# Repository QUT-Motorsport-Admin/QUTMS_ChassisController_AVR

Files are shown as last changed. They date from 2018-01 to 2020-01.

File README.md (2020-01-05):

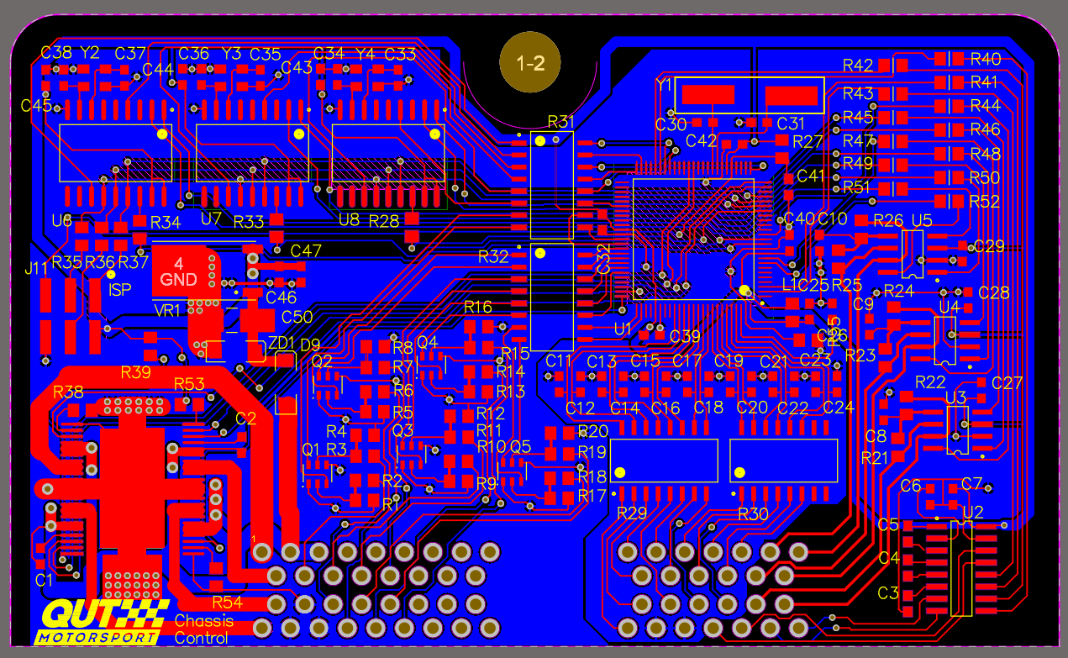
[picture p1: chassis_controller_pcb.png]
PCB Image


# Chassis Controller

The role of the chassis controller is to manage and coordinate all of the electrical systems on the car. At regular intervals it reads inputs and monitors devices on the car, checking they are responding to heartbeat messages within a specified time.

## Features

- 3 CANBUS interfaces using the MCP2515 controller
- 2 UART serial interfaces
- 14 analog inputs
- 9 digital inputs
- Dual 5A H-bridge throttle controller
- 60 pin MoTeC compatible connector

## System Architecture

### Serial Communication
The chassis controller has two UART interfaces, one which is dedicated to debugging. There is a [specification](https://docs.google.com/spreadsheets/d/1M0LFDXtBvufXvVOvwZmF34SnBRF86Ai6lYGNQQMeDdA/edit?usp=sharing "QUTMS_UART_Packet_Def") for a protocol to be used when the chassis controller is communicating with configuration software.

### Block Diagram

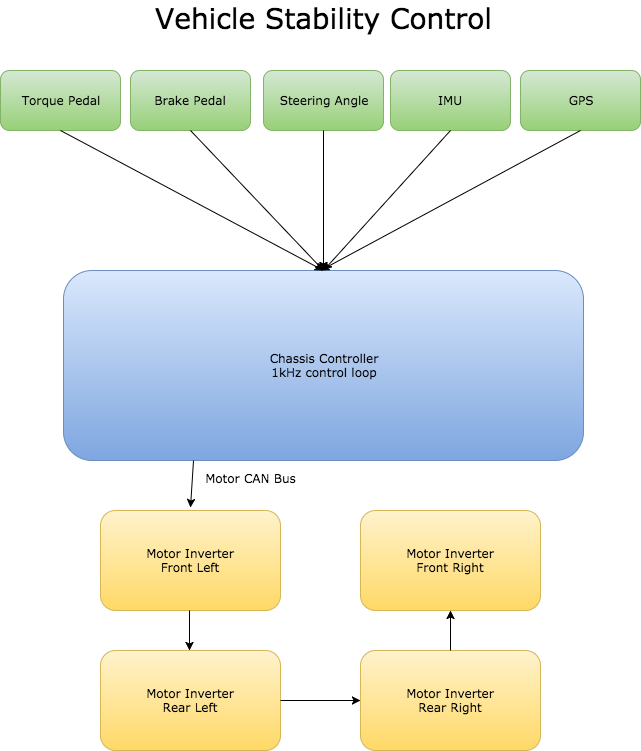
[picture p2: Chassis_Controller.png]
RoughOutline


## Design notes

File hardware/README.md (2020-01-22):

# Chassis Controller Hardware

## RS232 Serial Connection
Useful for getting debug output from the microcontroller. Uses a USB-to-RS232 adaptor and a custom DB9 to DTM-3P cable.

### Pinout

DB9 Connector

| Pin Number | Designation |
| --- | --- |
| 1 | |
| 2 | RX |
| 3 | TX |
| 4 | |
| 5 | Ground |
| 6 | |
| 7 | |
| 8 | |
| 9 | |

DTM-3P Connector

| Pin Number | Designation |
| --- | --- |
| 1 | Ground |
| 2 | TX |
| 3 | RX |

Remember that for serial to work RX and TX must be swapped or "crossed over" during the wiring.

## RS232 RF Modem

The XBee-PRO PKG-R® modules we have are a really simple way to make the debug connection to the chassis controller wireless. If working correctly they should be plug-n-play, so they're very easy to use.

The advertised range is around 12000m which should be enough to receive data from any point on a regular FSAE track. For example, lakeside raceway is around 250m from the furthest point on their small test track to the pits and the main track is around 600m to the furthest point to its respective pits.

The datasheet for this device is located in the datasheets folder of this repo.

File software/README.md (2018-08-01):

# Chassis Controller Software

The software for this system is one of the most important aspects to the system. It will be taking in all of the inputs throughout the system and congolerating them, and sending the required information for each of the other systems.

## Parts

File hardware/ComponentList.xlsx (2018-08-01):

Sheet: Chassis Controller
Component
Identifier | Type | Vlaue | Code |  | Footprint
C1 | Capacitor | 33nF |  |  | 0603
C10 | Capacitor | 10nF |  |  | 0603
C11 | Capacitor | 470nF |  |  | 0603
C12 | Capacitor | 470nF |  |  | 0603
C13 | Capacitor | 470nF |  |  | 0603
C14 | Capacitor | 470nF |  |  | 0603
C15 | Capacitor | 470nF |  |  | 0603
C16 | Capacitor | 470nF |  |  | 0603
C17 | Capacitor | 470nF |  |  | 0603
C18 | Capacitor | 470nF |  |  | 0603
C19 | Capacitor | 470nF |  |  | 0603
C2 | Capacitor | 33nF |  |  | 0603
C20 | Capacitor | 470nF |  |  | 0603
C21 | Capacitor | 470nF |  |  | 0603
C22 | Capacitor | 470nF |  |  | 0603
C23 | Capacitor | 470nF |  |  | 0603
C24 | Capacitor | 470nF |  |  | 0603
C25 | Capacitor | 100nF |  |  | 0603
C26 | Capacitor | 100nF |  |  | 0603
C27 | Capacitor | 100nF |  |  | 0603
C28 | Capacitor | 100nF |  |  | 0603
C29 | Capacitor | 100nF |  |  | 0603
C3 | Capacitor | 1uF |  |  | 0603
C30 | Capacitor | 18pF |  |  | 0603
C31 | Capacitor | 18pF |  |  | 0603
C32 | Capacitor | 18pF |  |  | 0603
C33 | Capacitor | 12pF |  |  | 0603
C34 | Capacitor | 12pF |  |  | 0603
C35 | Capacitor | 12pF |  |  | 0603
C36 | Capacitor | 12pF |  |  | 0603
C37 | Capacitor | 12pF |  |  | 0603
C38 | Capacitor | 12pF |  |  | 0603
C39 | Capacitor | 100nF |  |  | 0603
C4 | Capacitor | 1uF |  |  | 0603
C40 | Capacitor | 100nF |  |  | 0603
C41 | Capacitor | 100nF |  |  | 0603
C42 | Capacitor | 100nF |  |  | 0603
C43 | Capacitor | 100nF |  |  | 0603
C44 | Capacitor | 100nF |  |  | 0603
C45 | Capacitor | 100nF |  |  | 0603
C46 | Capacitor | 1uF |  |  | 0603
C47 | Capacitor | 1uF |  |  | 0603
C5 | Capacitor | 1uF |  |  | 0603
C50 | Capacitor | 1e-05 | 10 | 6 | 0603
C6 | Capacitor | 1uF |  |  | 0603
C7 | Capacitor | 1uF |  |  | 0603
C8 | Capacitor | 10nF |  |  | 0603
C9 | Capacitor | 10nF |  |  | 0603
D9 | Schottky Diode |  | B2100
J11 | ISP |  | 15910060
L1 | Inductor | 10mH
Q1 | Transistor |  | IMX1T110
Q2 | Transistor |  | IMX1T110
Q3 | Transistor |  | IMX1T110
Q4 | Transistor |  | IMX1T110
Q5 | Transistor |  | IMX1T110
R1 | Resistor | 4.7K | 470 | 1 | 0805
R10 | Resistor | 22K | 220 | 2 | 0805
R11 | Resistor | 22K | 220 | 2 | 0805
R12 | Resistor | 4.7K | 470 | 1 | 0805
R13 | Resistor | 4.7K | 470 | 1 | 0805
R14 | Resistor | 22K | 220 | 2 | 0805
R15 | Resistor | 22K | 220 | 2 | 0805
R16 | Resistor | 4.7K | 470 | 1 | 0805
R17 | Resistor | 4.7K | 470 | 1 | 0805
R18 | Resistor | 22K | 220 | 2 | 0805
R19 | Resistor | 22K | 220 | 2 | 0805
R2 | Resistor | 22K | 220 | 2 | 0805
R20 | Resistor | 4.7K | 470 | 1 | 0805
R21 | Resistor | 4.7K | 470 | 1 | 0805
R22 | Resistor | 4.7K | 470 | 1 | 0805
R23 | Resistor | 56 | 56R0 |  | 0805
R24 | Resistor | 56 | 56R0 |  | 0805
R25 | Resistor | 56 | 56R0 |  | 0805
R26 | Resistor | 56 | 56R0 |  | 0805
R27 | Resistor | 10K | 100 | 2 | 0805
R28 | Resistor | 1K | 100 | 1 | 0805
R29 | Resistor | 10000 | 4816P-1-103LF
R3 | Resistor | 22K | 220 | 2 | 0805
R30 | Resistor | 10000 | 4816P-1-103LF
R31 | Resistor | 1500 | 4816P-1-152LF
R32 | Resistor | 1500 | 4816P-1-152LF
R33 | Resistor | 1K | 100 | 1 | 0805
R34 | Resistor | 1K | 100 | 1 | 0805
R35 | Resistor | 0 | 0 | 0 | 0805
R36 | Resistor | 0 | 0 | 0 | 0805
R37 | Resistor | 0 | 0 | 0 | 0805
R38 | Resistor | 270 | 270 | 0 | 0805
R39 | Resistor | 270 | 270 | 0 | 0805
R4 | Resistor | 4.7K | 470 | 1 | 0805
R40 | Resistor | 1K | 100 | 1 | 0805
R41 | Resistor | 1K | 100 | 1 | 0805
R42 | Resistor | 1K | 100 | 1 | 0805
R43 | Resistor | 1K | 100 | 1 | 0805
R44 | Resistor | 1K | 100 | 1 | 0805
R45 | Resistor | 1K | 100 | 1 | 0805
R46 | Resistor | 1K | 100 | 1 | 0805
R47 | Resistor | 1K | 100 | 1 | 0805
R48 | Resistor | 1K | 100 | 1 | 0805
R49 | Resistor | 1K | 100 | 1 | 0805
R5 | Resistor | 4.7K | 470 | 1 | 0805
R50 | Resistor | 1K | 100 | 1 | 0805
R51 | Resistor | 1K | 100 | 1 | 0805
R52 | Resistor | 1K | 100 | 1 | 0805
R53 | Resistor | 270 | 270 | 0 | 0805
R54 | Resistor | 270 | 270 | 0 | 0805
R55 | Resistor | 10 | 10R0 |  | 0805
R6 | Resistor | 22K | 220 | 2 | 0805
R7 | Resistor | 22K | 220 | 2 | 0805
R8 | Resistor | 4.7K | 470 | 1 | 0805
R9 | Resistor | 4.7K | 470 | 1 | 0805
U1 | Microcontroller |  | ATMEGA1280-16AU
U2 | Dual EIA Driver/Receiver |  | MAX232
U3 | CAN Transceiver |  | A1040/C
U4 | CAN Transceiver |  | TJA1040
U5 | CAN Transceiver |  | A1040/C
U6 | CAN Controller |  | MCP2515
U7 | CAN Controller |  | MCP2515
U8 | CAN Controller |  | MCP2515
U9 | Motor Driver |  | MC33932VW
VR1 | Voltage Regulator |  | 78M05C
Y1 | Crystal |  | A160D69
Y2 | Crystal |  | TSX-3225
Y3 | Crystal |  | TSX-3225
Y4 | Crystal |  | TSX-3225
ZD1 | 36V Zenner Diode

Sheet: Steering Wheel
Component
Identifier | Type | Vlaue | Code |  | Footprint
C1 | Capacitor | 1uF |  |  | 0603
C10 | Capacitor | 100nF |  |  | 0603
C11 | Capacitor | 100nF |  |  | 0603
C12 | Capacitor | 0.33uF |  |  | 0603
C13 | Capacitor | 0.1uF |  |  | 0603
C2 | Not Present |  |  |  | 0603
C3 | Capacitor | 10uF |  |  | 0603
C4 | Capacitor | 18pF |  |  | 0603
C5 | Capacitor | 18pF |  |  | 0603
C6 | Capacitor | 100nF |  |  | 0603
C7 | Not Present |  |  |  | 0603
C8 | Capacitor | 10uF |  |  | 0603
C9 | Capacitor | 100nF |  |  | 0603
L1 | Inductor | 10mH |  |  | 0805
R1 | Resistor | 1K | 10 | 2 | 0805
R10 | Resistor | 4.7K | 470 | 1 | 0805
R11 | Resistor | 4.7K | 470 | 1 | 0805
R12 | Resistor | 4.7K | 470 | 1 | 0805
R13 | Resistor | 4.7K | 470 | 1 | 0805
R14 | Resistor | 4.7K | 470 | 1 | 0805
R15 | Resistor | 4.7K | 470 | 1 | 0805
R16 | Resistor | 4.7K | 470 | 1 | 0805
R17 | Resistor | 4.7K | 470 | 1 | 0805
R18 | Resistor | 4.7K | 470 | 1 | 0805
R19 | Resistor | 4.7K | 470 | 1 | 0805
R2 | Resistor | 1K | 10 | 2 | 0805
R20 | Resistor | 4.7K | 470 | 1 | 0805
R21 | Resistor | 4.7K | 470 | 1 | 0805
R22 | Resistor | 4.7K | 470 | 1 | 0805
R23 | Resistor | 4.7K | 470 | 1 | 0805
R24 | Resistor | 4.7K | 470 | 1 | 0805
R25 | Resistor | 4.7K | 470 | 1 | 0805
R26 | Resistor | 4.7K | 470 | 1 | 0805
R27 | Resistor | #VALUE! | DNP |  | 0805
R28 | Resistor | #VALUE! | DNP |  | 0805
R29 | Resistor | 100 | 100 | 0 | 0805
R3 | Resistor | 4.7K | 470 | 1 | 0805
R30 | Resistor | 100 | 100 | 0 | 0805
R31 | Resistor | 60 | 60R0 |  | 0805
R32 | Resistor | 60 | 60R0 |  | 0805
R33 | Resistor | 4.7K | 470 | 1 | 0805
R34 | Resistor | 4.7K | 470 | 1 | 0805
R35 | Resistor | 10K | 100 | 2 | 0805
R4 | Resistor | 4.7K | 470 | 1 | 0805
R5 | Resistor | 4.7K | 470 | 1 | 0805
R6 | Resistor | 4.7K | 470 | 1 | 0805
R7 | Resistor | 4.7K | 470 | 1 | 0805
R8 | Resistor | 4.7K | 470 | 1 | 0805
R9 | Resistor | 4.7K | 470 | 1 | 0805
U1 | Microcontroller |  | ATMEGA64M1-AU
U2 | Not Present
U3 | Not Present
U4 | CAN Transceiver |  | TJA1040/CM,118
VR1 | Voltage Regulator |  | MC33269ST-3.3T3G
VR2 | Voltage Regulaor |  | MIC5200-5.0YS
Y1 | Crystal | 16MHz | ABLS-16.000MHZ-D-4-T

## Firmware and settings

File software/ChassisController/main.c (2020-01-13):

#define F_CPU 16000000
#include "main.h"

uint16_t ignitionStateDebounceCount = 0;
uint8_t ignitionStateLock = 0;
uint8_t ignitionState = 0;

uint8_t isArmedState = 0;
uint8_t prevArmedState = 0;
uint8_t isSirenOn = 0;
static uint16_t sirenOnDuration = 2000; // 2000 milliseconds = 2 seconds
uint16_t sirenOnCount = 0;
static uint16_t preChargeOnDuration = 250; // 2000 milliseconds = 2 seconds
uint16_t preChargeOnCount = 0;
uint8_t isPreChargeOn = 0;
uint8_t isContactorHighOn = 0;

uint8_t isBrakeLightOn = 0;
uint8_t isCoolingPumpLeftOn = 1;
uint8_t isCoolingPumpRightOn = 1;
uint8_t isCoolingFanLeftOn = 1;
uint8_t isCoolingFanRightOn = 1;

uint8_t shutdownState = 0;

volatile uint8_t testError = 0;

char out[96] = {'\0'}; // CAN 1 SUFF
uint8_t inverterArray[8] = {0, 0, 0, 0, 0, 0, 0, 0};
uint8_t PDMarray[5] = {0, 0, 0, 0, 0};
uint8_t WheelArray[8] = {0, 0, 0, 0, 0, 0, 0, 0};

volatile uint8_t ouft = 0;

int main(void) {

    // Set Up
    firmware_init();
    timer_init();

    // Grab the state of the shutdown circuity
    shutdownState = 0;
    isSirenOn = 0;
    _delay_ms(500);
    // Enable Interupts
    sei();
    // Main Poll
    // ------------------------------------------------------------------------
    while(1) {

        //if(isCharAvailable() == 1)uart_process_byte(receiveChar());
        //uart1_puts("Hello World!\n");
    }

    // return 0; // Never return from an embedded program, does bad things if this ever triggers
}

/**
 * @brief Core system's timer, 1ms, core of the pseudo RTOS system
 */
void oneKHzTimer(void)
{
    static uint16_t CANheartbeatCountInverters = 0;			// Number of iterations for the inverter heartbeat trigger
    static uint16_t CANheartbeatCountWheel = 1;				// Number of iterations for the data heartbeat trigger
    static uint16_t CANheartbeatCountPDM = 2;				// Number of iterations for the power heartbeat trigger
    static uint16_t CANheartbeatCountShutdown = 3;			// Number of iterations for the power heartbeat trigger
    static uint16_t CANheartbeatCountAMU = 4;				// Number of iterations for the power heartbeat trigger

    // static uint8_t CanHeartbeatErrorInverters = 100;		// Time without successfull heartbeat for inverters
    // static uint8_t CanHeartbeatErrorData = 101;			// Time without successfull heartbeat for data
    // static uint8_t CanHeartbeatErrorPower = 102;			// Time without successfull heartbeat for power

    static uint8_t InputPedalThrottleCount = 5;				// Number of iterations for the throttle pedal heartbeat trigger
    static uint8_t InputPedalBrakeCount = 6;				// Number of iterations for the break pedel heartbeat trigger
    static uint8_t InputSteeringCount = 7;					// Number of iterations for the steering angle heartbeat trigger

    // Check the ignition button state
    // 1s debounce, IE hold for 50ms and if held, change state
    // ------------------------------------------------------------------------
    if(!(PINJ & (1 << PJ6))) // Checking Pin J6 (69)
    {
        ignitionState = 1; // Tracks that the ignition button is on
        if(ignitionStateDebounceCount++ > 1500) // If 1.5s has been counted
        {
            //If this is the first time though from a previous press
            if(ignitionStateLock == 0) {
                ignitionStateLock = 1;		// Disabled first run though after press
                isArmedState ^= 1;
                // If the armed state has just been turned on, activate the siren
                if(isArmedState == 1) {
                    led_toggle();
                    isSirenOn = 1;
                    isPreChargeOn = 1;
                } else {
                    led_toggle();
                    // Turning it all off just in case
                    isContactorHighOn = 0;
                    isPreChargeOn = 0;
                    isSirenOn = 0;
                }
            }

        }
    }
    else {
        ignitionState = 0; // Tracks that the ignition button is off
        ignitionStateLock = 0; // Re-enables the first run though after the timer has been reached
        ignitionStateDebounceCount = 0; // Resets the counter for time the button is pressed
    }

    // Additionally, see if the siren needs to sound that the HV is on
    if(isSirenOn == 1) { // Checks to see if the siren should be active
        if(sirenOnCount++ > sirenOnDuration) { // Counts up time, and if over allowance
            isSirenOn = 0; // Turn of siren
            sirenOnCount = 0;
        }
    }

    // Manage the Precharge time
    if(isPreChargeOn == 1) { // Checks to see if the siren should be active
        if(preChargeOnCount++ > preChargeOnDuration) { // Counts up time, and if over allowance
            isPreChargeOn = 0;
            preChargeOnCount = 0;
            isContactorHighOn = 1;
        }
    }

    // Gather all input pedals
    //------------------------------------------------------------------------

    uint8_t tmpInputVal;
    int8_t signedTmpInputVal;

    if(InputPedalThrottleCount > INPUT_TIME_PEDAL_THROTTLE)
    {
        //INPUT_accelerationPedal = (uint8_t)(a2d_10bitCh(5)); // Raw ADC sample
        if(INPUT_get_accelPedal(&tmpInputVal) == 0) {
            INPUT_accelerationPedal = tmpInputVal;
        }

        InputPedalThrottleCount = 0;
    }
    if(InputPedalBrakeCount > INPUT_TIME_PEDAL_BRAKE)
    {
        //INPUT_brakePedal = (uint8_t)(a2d_10bitCh(8)); // Raw ADC sample
        if(INPUT_get_brakePedal(&tmpInputVal) == 0) {
            INPUT_brakePedal = tmpInputVal;
        }
        InputPedalBrakeCount = 0;
    }
    if(InputSteeringCount > INPUT_TIME_STEERING)
    {
        //INPUT_steeringAngle = (uint16_t)(a2d_8bitCh(4)); // Raw ADC sample
        if(INPUT_get_steeringWheel(&signedTmpInputVal) == 0) {
            INPUT_steeringAngle = signedTmpInputVal;
        }
        InputSteeringCount = 0;
    }
    //if(INPUT_get_brakePressureBack(&tmpInputVal) == 0) {
    //    INPUT_brakePressureBack = tmpInputVal;
    //}
    //if(INPUT_get_brakePressureFront(&tmpInputVal) == 0) {
    //    INPUT_brakePressureFront = tmpInputVal;
    //}



    InputPedalThrottleCount++;
    InputPedalBrakeCount++;
    InputSteeringCount++;

    if (INPUT_accelerationPedal > 30 && INPUT_brakePedal > 30) {
        // if both pedals are pressed we don't want to go forward
        INPUT_accelerationPedal = 0;
    }

    // Brake light code
    if(INPUT_brakePedal > INPUT_PEDAL_BRAKE_LIGHT_ON) {
        isBrakeLightOn = 1;
    } else {
        isBrakeLightOn = 0;
    }

    // Creating CANBUS Packet data for transmission
    //------------------------------------------------------------------------

    inverterArray[0] = INPUT_accelerationPedal;
    inverterArray[1] = INPUT_brakePedal;
    inverterArray[2] = INPUT_steeringAngle;
    inverterArray[3] = isArmedState;
    inverterArray[4] = sirenOnCount;
    inverterArray[5] = isContactorHighOn << 7 | isPreChargeOn << 6 | isSirenOn << 5 | isBrakeLightOn << 4 |
                       isCoolingFanLeftOn << 3 | isCoolingPumpLeftOn << 2 | isCoolingFanRightOn << 1 | isCoolingPumpRightOn | 0; // General State

    WheelArray[0] = INPUT_accelerationPedal;
    WheelArray[1] = INPUT_brakePedal;
    WheelArray[2] = INPUT_steeringAngle;
    WheelArray[3] = isArmedState;
    WheelArray[4] = sirenOnCount;
    WheelArray[5] = isContactorHighOn << 7 | isPreChargeOn << 6 | isSirenOn << 5 | isBrakeLightOn << 4 |
                    isCoolingFanLeftOn << 3 | isCoolingPumpLeftOn << 2 | isCoolingFanRightOn << 1 | isCoolingPumpRightOn | 0; // General State

    // Fill PDM Array
    PDMarray[0] = isContactorHighOn << 7 | isPreChargeOn << 6 | isSirenOn << 5 | isBrakeLightOn << 4 |
                  isCoolingFanLeftOn << 3 | isCoolingPumpLeftOn << 2 | isCoolingFanRightOn << 1 | isCoolingPumpRightOn | 0; // General State
    PDMarray[1] = 100; //
    PDMarray[2] = 100; //
    PDMarray[3] = 100; //
    PDMarray[4] = 100; //

    // CANBUS Sending
    // Send CAN heartbeats -> Inverters: 100Hz, Data: 100Hz, Power: 20Hz
    // 100Hz = 1 / 100 = 0.01s = 10ms, 20Hz = 1 / 20 = 0.05s = 50ms
    //------------------------------------------------------------------------

    if(CANheartbeatCountInverters >= CAN_HEARTBEAT_TIME_INVERTERS) {
        // Reset inverter heartbeat counter
        CANheartbeatCountInverters = 0;
        // Send inverter system heartbeat 0b0100100000000000000000000011110
        CAN_send(TRACTIVE_CAN, 8, inverterArray, HEARTBEAT_INV_ID);

    }
    if(CANheartbeatCountWheel > CAN_HEARTBEAT_TIME_WHEEL) {
        // Reset data heartbeat counter
        CANheartbeatCountWheel = 0;
        // Send data system heartbeat
        CAN_send(DATA_CAN, 8, WheelArray, HEARTBEAT_WHEEL_ID | 1);
    }
    if(CANheartbeatCountPDM > CAN_HEARTBEAT_TIME_PDM) {
        // Reset power heartbeat counter
        CANheartbeatCountPDM = 0;
        // isContactorHighOn ^= 1;
        // Send power system heartbeat (5 bytes in PDM array)
        CAN_send(POWER_CAN, 5, PDMarray, HEARTBEAT_PDM_ID | 1);
    }

    if(CANheartbeatCountAMU > CAN_HEARTBEAT_TIME_AMU) {
        // Reset power heartbeat counter
        CANheartbeatCountAMU = 0;
        // Send shutdown heartbeat (dont care what for now)
        // CAN_send(POWER_CAN, 5, PDMarray, HEARTBEAT_AMU_ID | 1);

        //UART_formTestPacket();

        // OUTPUT BRAKE AND ACCEL PEDALS TO SERIAL
        char tempString[4] = {0};
        itoa(INPUT_brakePedal, tempString, 10);
        for (int i = 0; i < 4; i++) uart_putc(tempString[i]);

        uart_putc('\t');

        itoa(INPUT_accelerationPedal, tempString, 10);
        for (int i = 0; i < 4; i++) uart_putc(tempString[i]);

        uart_putc('\n');

    }

    // the adding commented to test a counting system in the inverters if statement
    CANheartbeatCountInverters++;
    CANheartbeatCountWheel++;
    CANheartbeatCountPDM++;
    CANheartbeatCountShutdown++;
    CANheartbeatCountAMU++;

    // CAN Error counts -> Missing Receives
    // ------------------------------------------------------------------------

    // if(CanHeartbeatErrorInverters > CAN_HEARTBEAT_ERROR_DELAY)
    // {
    //     throw_error_code(ERROR_LEVEL_WARN, ERROR_CANBUS_1_NO_RESPONSE);
    // }
    // if(CanHeartbeatErrorData > CAN_HEARTBEAT_ERROR_DELAY)
    // {
    //     throw_error_code(ERROR_LEVEL_WARN, ERROR_CANBUS_2_NO_RESPONSE);
    // }
    // if(CanHeartbeatErrorPower > CAN_HEARTBEAT_ERROR_DELAY)
    // {
    //     throw_error_code(ERROR_LEVEL_WARN, ERROR_CANBUS_3_NO_RESPONSE);
    // }
    // CanHeartbeatErrorInverters++;
    // CanHeartbeatErrorData++;
    // CanHeartbeatErrorPower++;

}

// -------------------------------------------------- Interrupt Service Routines --------------------------------------------------

/**
 * @brief Called whenever the 1Khz timer triggers
 */
ISR(TIMER0_COMPA_vect)
{
    oneKHzTimer();
}

ISR(TIMER1_COMPA_vect)
{

}

/**
 * @brief Called whenever CANBUS 1 interupt is triggered
 *        * When ever there is data waiting in CAN 1
 */
ISR(INT1_vect) {
    // Details about the message we're attempting to pull from the CAN bus
    uint8_t data[8];
    uint32_t ID;
    uint8_t numBytes;
    // Get the data from the CAN bus and process it
    CAN_pull_packet(TRACTIVE_CAN, &numBytes, data, &ID);
    led_toggle();

    // If the data packet is crap
    // throw_error_code(ERROR_LEVEL_WARN, ERROR_CANBUS_1_RESPONSE_MALFORMED);
    //out++;

    //sprintf(out, "%x,%x,%x,%x,%x,%x,%x,%x", data[0], data[1], data[2], data[3], data[4], data[5], data[6], data[7]);
}

/**
 * @brief Called whenever CANBUS 2 interupt is triggered
 *        * When ever there is data waiting in CAN 2
 */
ISR(INT0_vect)	{
    // Details about the message we're attempting to pull from the CAN bus
    uint8_t data[8];
    uint32_t ID;
    uint8_t numBytes;
    //led_toggle();
    // Get the data from the CAN bus and process it
    CAN_pull_packet(POWER_CAN, &numBytes, data, &ID);

    // If the data packet is crap
    // throw_error_code(ERROR_LEVEL_WARN, ERROR_CANBUS_2_RESPONSE_MALFORMED);

}

/**
 * @brief Called whenever CANBUS 3 interupt is triggered
 *        * When ever there is data waiting in CAN 3
 */
ISR(PCINT0_vect) {
    // Details about the message we're attempting to pull from the CAN bus
    uint8_t data[8];
    uint32_t ID;
    uint8_t numBytes;
    //led_toggle();
    // Get the data from the CAN bus and process it
    CAN_pull_packet(DATA_CAN, &numBytes, data, &ID);

    // If the data packet is crap
    // throw_error_code(ERROR_LEVEL_WARN, ERROR_CANBUS_3_RESPONSE_MALFORMED);



}

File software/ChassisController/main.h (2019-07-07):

#define F_CPU 16000000

#include <avr/io.h>
#include <avr/interrupt.h>
#include <stdio.h>
#include <stdlib.h>
#include <string.h>
#include <util/delay.h>
#include "MCP2515.h"
#include "uart.h"
#include "a2d.h"
#include "chassisInit.h"
#include "chassisInput.h"
#include "chassisUART.h"
#include "chassisLED.h"
#include "chassisCAN.h"
#include "chassisError.h"




#define HEARTBEAT_INV_ID		0x04000000
#define	HEARTBEAT_AMU_ID		0x0A000000
#define HEARTBEAT_PDM_ID		0x09000000
#define HEARTBEAT_SHUTDOWN_ID	0x08800000
#define HEARTBEAT_WHEEL_ID		0x08400000

// Variables used in the 1kHz CAN heartbeat loop
#define CAN_HEARTBEAT_TIME_INVERTERS (100)   // Defines the 10ms (100Hz) for the inverter trigger
#define CAN_HEARTBEAT_TIME_DATA (100)        // Defines the 10ms (100Hz) for the data trigger
#define CAN_HEARTBEAT_TIME_PDM (100)			// Defines the 50ms (20Hz) for the power trigger
#define CAN_HEARTBEAT_TIME_WHEEL (100)       // Defines the 50ms (20Hz) for the power trigger
#define CAN_HEARTBEAT_TIME_SHUTDOWN (100)   // Defines the 100ms (10Hz) for the power trigger
#define CAN_HEARTBEAT_TIME_AMU (100)			// Defines the 50ms (20Hz) for the power trigger

#define CAN_HEARTBEAT_ERROR_DELAY (110)     // Milliseconds without return heartbeat, must be slightly larger than largest heartbeat time x2

#define INPUT_TIME_PEDAL_THROTTLE  (10)     // Defines the 10ms (100Hz) for the input send trigger
#define INPUT_TIME_PEDAL_BRAKE  (10)        // Defines the 10ms (100Hz) for the input send trigger
#define INPUT_TIME_STEERING  (10)			// Defines the 10ms (100Hz) for the input send trigger
#define INPUT_TIME_TEMP (100)               // Defines the 100ms (10Hz) for the input send trigger

#define CAN_INPUT_SEND_DELAY (10)           // Defines the 200ms (5Hz) for the input send trigger

#define CAR_ARM_HV (1)                      // Used to set the car's armed state to high
#define CAR_DISARM_HV (0)                   // Used to set the car's armed state to low
extern uint8_t isArmedState;					// Stores the car's armed state
extern uint8_t ignitionState;				// Stores the car's ignition switch/button state

extern uint8_t shutdownState;				// Stores the car's current state of its shutdown circuity

extern uint8_t PDMarray[5];

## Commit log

2018-01-30 Initial Content Commit
    [CC_v1_final.PcbDoc]
2018-03-05 Fixed formatting issues. Started commenting functions
    [MCP2515.c, MCP2515_CC.c, MCP2515_CC.h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]
2018-06-23 Added Chassis EEPROM Read/Write Functionality
2018-06-23 Updated EEPROM Code Comments with Example Code
    Also corrected datasheet sample code refrence to mention the section of the ATmega1280 datasheet (it previously mentioned the pages of the ATmega64M1 datasheet).
2018-06-23 Data received from CAN bus is now through interrupts instead of polling
2018-06-23 Modified existing error throws to use updated function call
    [main.c]
2018-06-23 Added some potential error codes
    [chassisError.h]
2018-06-24 Updated error throwing to allow including the part number (Gearbox 1, Radiator 2 etc.) in output message
    [chassisError.c, chassisError.h]
2018-06-24 Updated calls to send error message, and error swich case template
    [chassisError.c]
2018-06-24 Added Defines for Chassis Settings Stored in EEPROM
2018-06-24 Changed Leftover chassisUART.h #include to chassisEEPROM.h in chassisEEPROM.c
2018-06-24 Added Error Codes and Cases
    [chassisError.c, chassisError.h]
2018-06-24 Added Doxygen Comments to Chassis EEPROM Code
2018-06-24 Additional Doxygen Added to uart.h
2018-06-24 Added Battery Errors
2018-06-26 Updated Doxygen comments on Error and Input include files. Added QUTMS logo to Doxyfile.
    [chassisError.h, chassisInput.c, chassisInput.h]
2018-06-26 Added Doxygen Comments to Error Codes
    [chassisError.h]
2018-07-08 Namespaced all error related functions and defines
    [chassisError.c, chassisError.h]
2018-07-12 Added all input filtering and functions, now building fully
2018-07-21 Working ADC, broken UART
    [chassisInit.c, chassisInput.c, chassisInput.h]
2018-07-21 Fixed names & convetions, includes, headers and some algorithms
    [chassisInput.c, chassisInput.h, chassisUART.c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]
2018-07-22 Implemented ignition button and armed states, sent through UART
2018-07-22 Added in system states, ignition button and debounce code, PDM systems and extra error codes
    [chassisError.c, chassisError.h, chassisUART.c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]
2018-07-26 Fixed brake pedal read, added PDM comms, added steering read
    [MCP2515.c, chassisInit.c, chassisInput.c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]
2018-07-31 Latest work from weekend's efforts, mostly in the merge 2 folder containing an atmel studio project. Communicates on all 3 can buses, turns pdm circuits on and off, sends to the wheel, sends torque t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
2018-08-01 Component List
    The complete component list for the chassis controller and steering wheel
    [ComponentList.xlsx]
2019-01-17 Enable Ignition Button on PCINT15
2019-01-18 changed UART_send_data to UART_sendPacket. Added switch case for shutdown state error handling.
    [chassisError.c, chassisError.h]
2019-01-18 fixed errors in shutdown_probe, shutdown_state and removed errors with multiple definitions of STOP_FLAGS.
    [chassisError.c, chassisError.h]
2019-01-21 Reimplemented shutdown_state to handle multiple error states.
    [chassisError.c, chassisError.h]
2019-01-21 Fixed incorrect message length values.
    [chassisError.c]
2019-02-18 led light change
2019-02-20 Added in pedal fixes, brake lights, siren functionality, ignition switch, and putting that down various can busses
    [chassisInput.c, chassisInput.h, main.c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]
2019-02-20 Fixed up mergeing a little
    [chassisUART.c, main.h]
2019-02-25 Working PDM, Steering wheel, ADC on Pedal and Steering wheel
2019-06-28 Added in new input code to deal with shifting pedals, auto calibrates on start up and uses offset. Added pre-chrage functionality
2020-01-04 added chassis controller pcb image
2020-01-07 Fix compiler warning. This may have been causing issues
    [chassisInit.c]
2020-01-07 fix another implicit definition warning
    [chassisInput.h]
2020-01-07 The board now has external pull-downs to make the pedals fail off.
    [chassisInit.c]
2020-01-08 Re-factor accelerator pedal input. Remove the auto-calibrating function because it's not needed.
2020-01-08 Refactor throttle and steering inputs
2020-01-12 Fix formatting and update comments
    [chassisInput.c]
2020-01-12 Clean up led functions and comments
2020-01-13 Added micro-controller to schematic
    [CC_v1_final.PcbDoc, MCU.SchDoc]
2020-01-13 Add project file
    [ChassisController.PrjPcb]
2020-01-13 Change PCB file name
    [CC_v1_final.PcbDoc, ChassisController.PcbDoc, ChassisController.PrjPcb]
